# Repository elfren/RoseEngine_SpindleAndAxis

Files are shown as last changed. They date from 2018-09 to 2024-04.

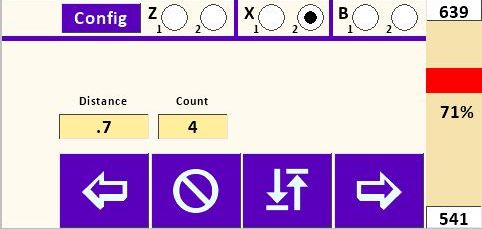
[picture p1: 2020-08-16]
MDF Rose Engine 2.0/Nextion Multiple Stepper Control User's Guide/Images/Nextion-Move2.jpg

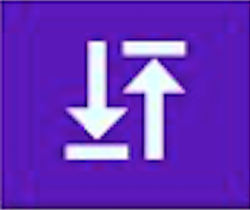
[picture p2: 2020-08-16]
MDF Rose Engine 2.0/Nextion Multiple Stepper Control User's Guide/Images/ButtonMove-Return.png

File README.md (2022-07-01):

# RoseEngine_SpindleAndAxis
Drive Rose Engine steppers for the spindle and up to 4 additional axes.

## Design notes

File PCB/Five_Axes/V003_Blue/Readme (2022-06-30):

This pcb uses several surface mount components (see BOM).
https://www.seeedstudio.com/5-axes-Rose-Engine-and-CNC-g-1367637

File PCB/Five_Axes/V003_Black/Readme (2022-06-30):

This 5 axes Rose Engine and CNC controller uses all through hole components.
SeeedStudio: https://www.seeedstudio.com/Rose-Engine-5-motor-driver-g-1364994
OshPark: https://oshpark.com/shared_projects/8f3nmKMy

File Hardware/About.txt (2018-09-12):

GT2-5mm 108 tooth pulley designed for CNC milling.

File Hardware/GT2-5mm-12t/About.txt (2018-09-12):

Print at 100% infill using ABS filament.

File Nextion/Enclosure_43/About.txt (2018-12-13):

Print at 30% to 100% infill.
Note: The bezel only has one hole created for the Nextion.  The other three need to be drilled (2.5mm) and all four should be tapped (3mm).

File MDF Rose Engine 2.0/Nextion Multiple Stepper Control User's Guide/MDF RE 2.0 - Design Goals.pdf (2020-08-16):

# MDF Rose Engine Lathe 2.0

# with Stepper Motor Drive

# Design Goals

## Version 1.0 04 July 2020

## MDF Rose Engine 2.0 – Design Goals

This document is intended to outline the design goals around which the machine is specified.

If you have any questions, please contact us at ColvinTools@Gmail.com.

Good luck.

Rich Colvin & Jack Zimmel

### Table of Contents

## Guiding Principles

### General – Target User

1. The target user for the MDF rose engine lathe is
a. An experienced wood turner, with
b. The basic woodworking skills that would have been garnered in shop class.
2. The design will ensure it can be built by the woodworker:
a. Using a kit of parts we will provide,
b. Possessing basic woodworking skills, and
c. Using tools which can reasonably be expected to be available or easily accessible.

### General – Overall Design

1. The intent is to stay consistent with the original overall design outlined by Jon Magill, especially the designs built into the rosettes.
2. The design will continue to use MDF as the primary building material for the headstock and base.
3. The design will include commonly implemented updates to the original design, including:
a. Stepper motor for the spindle drive,
b. Metal sheet on the lathe’s bed,
c. Magnetic hold-downs (MagSwitches) for locking the cross slide into position on the lathe bed,
d. Front and rear rubbers, and
e. Amplitude adjusting (front rubbers only).
4. The design will not include previously offered features which would make the overall design cumbersome or expensive. In particular, hand cranking capabilities will not be included,
5. The design will provision for known future options / expansions:
a. Multiple stepper motors with controls for the multiple stepper motors, and
b. Pumping on the spindle.

### Kit Offered for Sale

1. The design should enable a complete rose engine lathe to be built from a kit for less than $2,000. And the design should be designed to be lower if the user opts to make their own parts.
2. The kit offered for sale will provide options which, in total, will supply the hobbyist with all the parts needed (including the MDF).
a. Using standard, off-the-shelf parts, with a conscious decision being made when customized parts are to be used,
b. Sourcing parts from vendors likely to provide the parts for a reasonable time into the future (i.e., minimizing rework of the designs), and
c. Sourcing more expensive parts from vendors who will accommodate drop-shipments. This reduces the investment in inventory for the provider of the kits.
3. The kit offered for sale will provide options where it makes reasonable sense. Option selections include:
a. Spindle drive option – Everything needed to drive the spindle with a stepper motor (stepper motors allow the spindle's speed to be slowed down to multiple minutes per revolution)
i. Or allow the builder to build or source their own approach, and
ii. Also, provision existing MDF rose engine lathe owners to add this to their system.
b. Cutting frame option - Enabling the builder to
i. Select a universal cutting frame with an integrated motor,
ii. Select a universal cutting frame with an overhead drive,
iii. Make their own cutting (or drilling frame), or
iv. Source one from a different source.
c. Tool holder (cross slide and tool post) option – Enabling the builder to
i. Select a pre-defined set of cross slide, quick-change tool post, and tool holders (AXA), or
ii. Source one from a different source.
d. Case Option – Enabling the builder to
i. Select a pre-cut MDF kit with all the pieces for the body and headstock, already cut to size and ready for assembly
ii. Source and build the case and headstock on their own.

## Design Criteria

### Headstock

1. The distance from the center of the rocking pivots to the center of the spindle shall be 12 inches. The rosettes are designed around this.

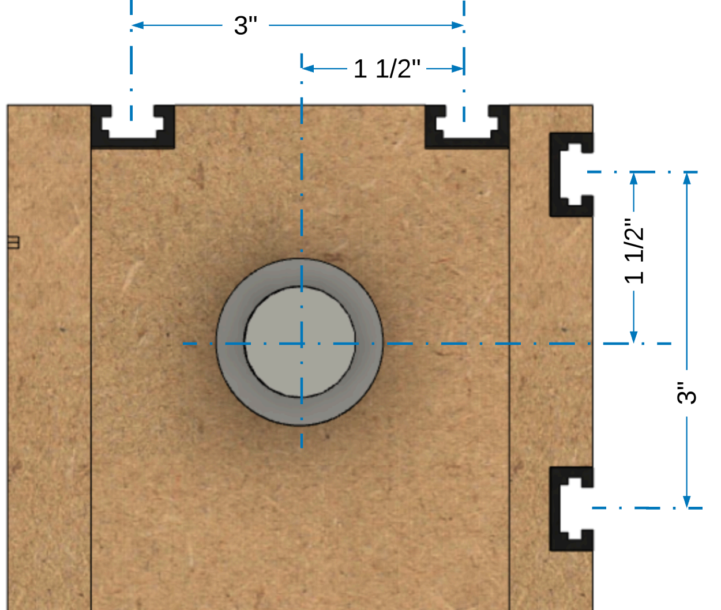
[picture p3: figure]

2. The rocking pivot points are to be aligned so
that the rotation of the headstock is fully
aligned with the rotation of the spindle.
3. T-Tracks will be implemented on the headstock for standardized add-ons.
a. The T-Tracks will be aligned to be parallel with the spindle,
b. The center of each T-Track shall be 1-1/2” from the center of the spindle (as shown to the right),
c. There shall be two T-Tracks on the top of the headstock, and
d. There shall be two T-Tracks on the rear of the headstock.

### Base

1. The lathe’s bed shall be sized to accommodate the
attachment of a 24” x 24”
sheet of steel.
2. The sheet of steel on the lathe bed shall be minimally 16
gauge, and the design shall be able to accommodate
upgrading that sheet to a
thickness of 1/8”.
3. The lathe’s bed (B1 / B1A) shall:
a. Overhang the base by
2” on the front, back,
and right sides (in the

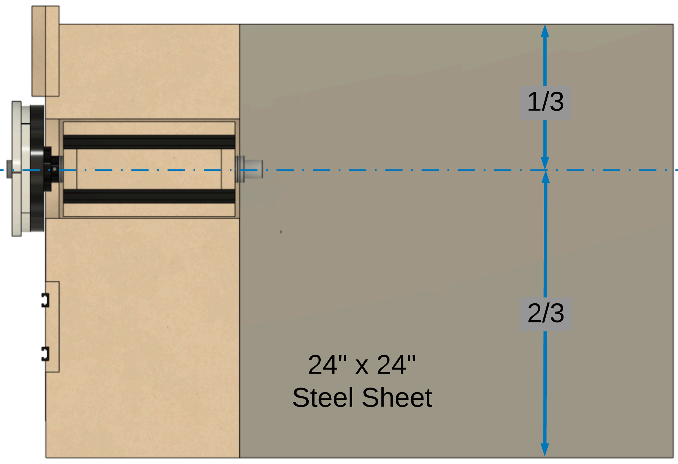
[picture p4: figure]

picture to the right, those are the right, top, and left sides),
b. Be flush against the left side (B3 / the rubber support post), and
c. Be positioned front-to-back so that it has approximately 1/3 behind the spindle’s axis of rotation, and 2/3 in front of that axis.

### Spindle Drive

1. The spindle drive shall use a NEMA 23 stepper motor.
2. The controls will be implemented the Teensy/Nextion controls.
a. The power supply (EDR-120-24) will be expandable as necessary for future options.
b. The design will be based on the DM542T motor drivers; however, the user could opt to use other drivers such as the DRV8825.
3. The connectors for the stepper motors and aviation plugs with 4-wire connections.

### Other

1. Tool holding is designed around the AXA standard.

To the extent that material may appear to be infringed, we assert that such alleged infringement is permissible under fair use principles in U.S. copyright laws. If you believe material has been used in an unauthorized manner, please contact me at ColvinTools@Gmail.com.

Portions of this document are copyrighted by Jon Magill and are used with his permission.

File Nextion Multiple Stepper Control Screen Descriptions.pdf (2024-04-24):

## Nextion Multiple Stepper Control Screen Descriptions

V: 3.1.0

Splash Screen

Purpose: Initialize program

Buttons explanation: Touching one of the top or bottom row buttons will take you to that screen.

Main Screen

Purpose: Allows direct control of spindle speed and direction and auxiliary axis speed and direction independent of one another. Typically used for continuous spindle and/or continuous Axis motion (turning or facing cuts, continuous rose engine patterns on cylindrical or face surfaces., etc.).

Buttons explanation:
- “” (Counterclockwise) and “” (Clockwise) rotational arrows indicate direction of the Spindle. “”(In) and “”(Out) indicates direction of the selected axis. Rotation/movement continues until “” (Stop) is pushed.

- Right and left speed bars (for Spindle and Axes, respectively, are shown as a percentage of maximum speeds set for “Main” and “Z, X, M3 or M4 Axes”. Max speed and acceleration entry fields are shown at the top and bottom of each speed bar. They are in stepper steps per second.
- “ “(Return): Returns the spindle or the selected axis to the start point of the previous operation.
- Synchro: Runs the spindle and M3 synchronously at the specified percentages. Negative number runs the spindle and M3 in opposite directions.

Number Pad Screen

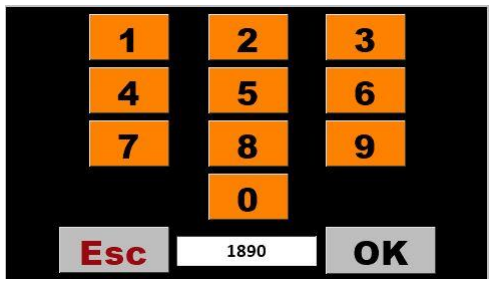
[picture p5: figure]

Purpose: This screen appears whenever any numerical value on any screen is tapped. Revise the number in the box by tapping the box multiple times to “backspace” over each digit or decimal point, and then re-enter the new value using the number pad buttons. Pressing “OK” saves the number back to the value box on the previous screen and returns user to that screen.

Synchronization Screen

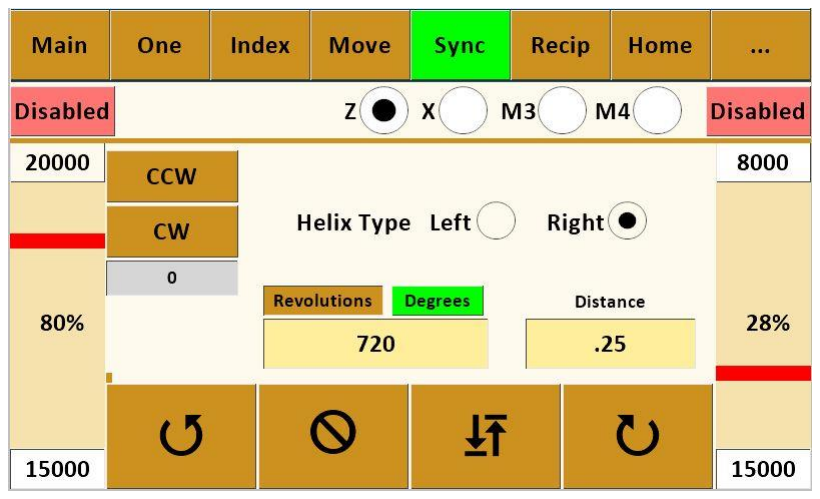
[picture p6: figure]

Purpose: Synchronizes the Spindle and Auxiliary Axis to produce helical patterns or threads on cylindrical surface of workpiece or to produce spirals on a face surface.

Buttons explanation:
- “Left” and “Right” determine whether helix runs clockwise or counterclockwise on the piece.
- “CW” (Clockwise) and “CCW” (Counterclockwise) index the spindle for the next cut path – either clockwise or counterclockwise per user design. Amount the spindle will index uses the value in “Size” set in the box on the Index #1 Screen (this value could be either in divisions of a circle or degrees depending upon which option is toggled on Index #1 Screen).
- “Revolutions or Degrees” variable value determines how far around the piece the helix will travel based on the spindle rotating. The value of 4 illustrated will rotate spindle 4 revolutions while the value 720 will rotate the spindle 720 degrees.

- “Distance” variable value determines the cut length (amount of Z axis movement) and is dependent upon value entered in Setup Screen for “Distance/360”.
- Right and left speed bars (for Spindle and Axis, respectively, are shown as a percentage of maximum speeds set on the Configuration Screen for “Sync” and “Z Axis”, respectively. Note that slowest value on speed bars will “control” the other value.
- “”(In) and “”(Out) determine whether cut is made toward or away from headstock. Pattern will run the pre-determined “Distance” and then stop and wait for return direction instruction. User chooses whether to cut in both directions or retract cutter and return to start without cutting.
- “ “(Return): Returns both the spindle and the axis to the start point of the previous operation.
- See appendix for procedure for using the Synchronization Screen for thread cutting.

Reciprocation – Axial

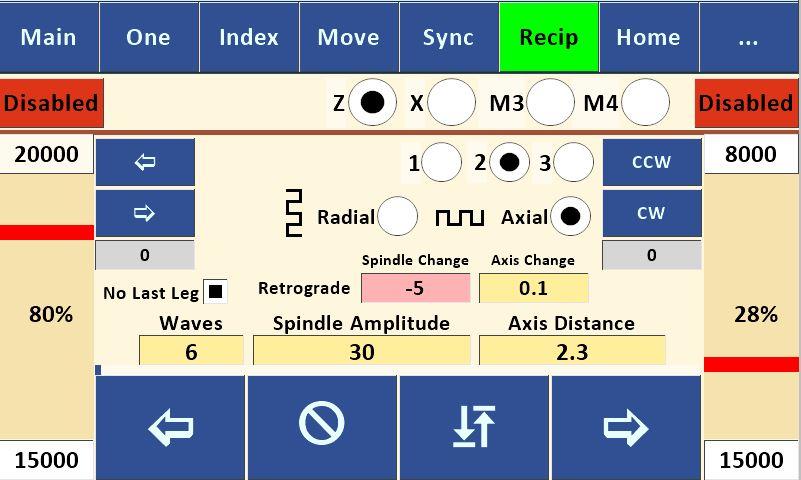
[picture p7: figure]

Purpose: Synchronizes Spindle and Auxiliary Axis to produce a reciprocating pattern along the longitudinal cylindrical surface of workpiece: It works by reversing spindle direction alternately while Z or X axis continues in the same direction.

Buttons explanation

- “1” Pattern is an equal angle on the up and down legs.
- “2” Pattern is a square wave.
- “3” Pattern is a like a sawtooth. The up leg is angled, the down leg is straight down.
- “CW” (Clockwise) and “CCW” (Counterclockwise) index the spindle for the next reciprocating cut path – either clockwise or counterclockwise per user design or desire. Amount the spindle will index uses the value set in the “Size” box on the Index #1 Screen (this value could be either in divisions of a circle or degrees depending upon which option is toggled on Index #1 Screen).
- “Wave Count” variable sets number of individual waves /\ to be cut along the cylinder.
- “Spindle Amplitude” variable sets “height” of each wave in degrees of rotation.
- Retrograde changes the length of each leg by the specified amount either plus or minus.
- No Last Leg removes the final leg of a Square wave (pattern 2).
- “Axis Distance” variable determines the cut length for entire pattern (amount of Z, X, M3, or M4 axis movement) and is dependent upon value entered in Setup Screen for “Distance/360”.
- “”(In) and “”(Out) determine whether cut is made toward or away from headstock. Note that “”(In) starts with a downward move and “”(Out) starts with an upward move (test your individual machine and apparatus to verify – your results may vary). Pattern will run the pre-determined “Axis Distance” and then stop and wait for return direction instruction. User chooses whether to cut in both directions or retract cutter and return to start without cutting.

- “ “(Return): Returns both the spindle and the axis to the start point of the previous operation.

Reciprocation –Radial

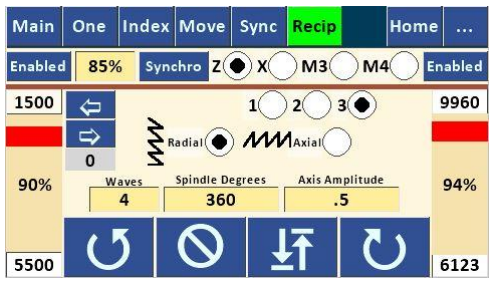
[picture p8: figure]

Purpose: Synchronizes Spindle and Auxiliary Axis to produce a sharp-pointed reciprocating pattern along the circumferential surface of a cylindrical workpiece: It works by alternately reversing Z or X axis direction while spindle continues rotating in the same direction.

Buttons explanation
- To navigate to this screen, start with “Recip” and toggle from Axial to Radial.
- “1” Pattern is an equal angle on the up and down legs.
- “2” Pattern is a square wave.
- “3” Pattern is a like a sawtooth. The up leg is angled, the down leg is straight down.
- Small “”(In) and “”(Out) move the Z or X axis to the next pattern starting position. Z or X axis movement will be the value of “Distance” set on the Move Screen for that axis.
- “Return” button rotates the spindle to the pattern start point.
- “Acceleration” and “Speed” values for this screen are set here for both Spindle, Z, and X axes. See notes on value limitations under Configuration Screen explanation. Because of synchronization of the spindle and Z or X axis speeds, one of the maximum speeds will control the other.
- “Wave Count” variable sets number of individual waves ( > ) to be cut along the cylinder.
- “Spindle Degrees” variable sets the circumferential distance around the cylinder for the total pattern. Entering 360 would wrap the pattern all the way around the cylinder; entering 90 would condense the whole pattern around just 90 degrees of the cylinder.
- “Axis Amplitude” variable sets “height” (distance along Z, X, M3 or M4 axis) of each wave and is dependent upon value entered in Setup Screen for “Distance/360”.
- | Large “”(In) and “”(Out) buttons determine the direction of cut around the spindle. | Pattern will run the
pre-determined “Spindle Degrees” then stop and wait for return direction instruction. User chooses whether to cut in both directions (either on the same cut path or on subsequent path) or retract cutter and return to the origin point without cutting.
- “ “(Return): Returns both the spindle and the axis to the start point of the previous operation.

One Screen (Single Stepper Screen)

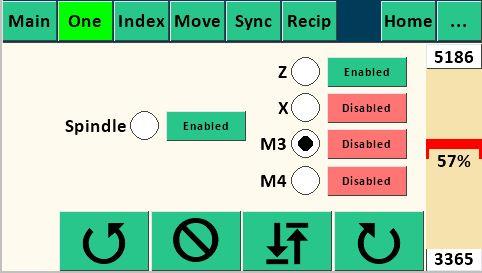
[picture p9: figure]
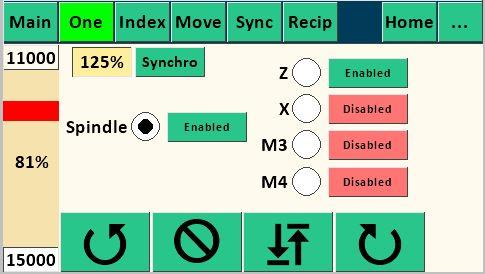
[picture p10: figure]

Purpose: Allows control of either the spindle or a single axis speed and direction. Useful for secondary spindle operation such as higher or lower speed functions than the Main Screen.
Buttons explanation
- “Enabled” shows status (either “Enabled” or “Disabled”) of either Spindle stepper motor or an Axis stepper motor as selected. If enabled, the motor is in locked status; if disabled, the selected motor can be repositioned. Default is “Disabled”. Primary use for these buttons is to lock the spindle or axis while performing another operation.
- “” (Counterclockwise) and “” (Clockwise) rotational arrows indicate direction of the Spindle .“”(In) and “”(Out) buttons indicate direction of an axis. Movement continues until “Stop” is pushed.
- Speed bar is shown only for the selected axis or spindle.

Index Screen

Purpose: Allows indexing spindle for use in index work or other uses. Buttons explanation

- 1-5: Individual indexes
- “Div” radio button sets the indexing to number of divisions of a full rotation, toggling to “Deg” sets the indexing to number of degrees.

- “Index” box shows current completed index
- “Next Index” shows ID of the next index. It will show lower ID if the CW button was last touched and higher if CCW button was touched
- Speed bar is shown as a percentage of maximum speeds set on the Configuration Screen for “Index”.
- “Divisions” of a circle or “Degrees”, depending upon which is toggled. Note that the value of the selected index (1 through 5) is used by the “CW” and “CCW” indexing movements on the Synchronization Screen and the Reciprocation – Axis Screen in either “Divisions” or “Degrees”, depending upon which is toggled.
- M3 and M4 will only be shown if they are set to Radial on their respective configuration screens.

Index Screen with file dropdown open

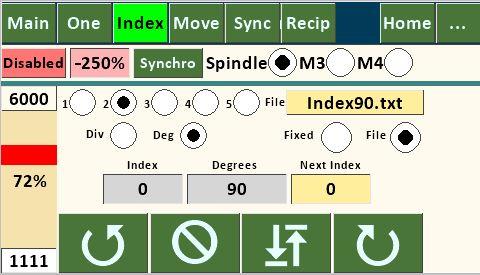
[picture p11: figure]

Purpose: Allows variable index sizes to be retrieved sequentially from a file stored on a microSD card. This feature could be used to place evenly spaced features (such as barleycorns) around the circumference of an ellipse (i.e. equal division of the ellipse), with the angular movement in degrees precalculated using a CAD program.

Selecting the filename text box will open a dropdown list of files located on the microSD card. Use the Up and Down arrows to traverse the file list. While the dropdown list is active, all other controls on the page are disabled. The dropdown list can be closed either by selecting a file, or by touching the Filename textbox. Each Index may have its own file.

The file format is ASCII text (numbers, letters, and decimal only) with each number on a new line, saved to the microSD card using a separate computer. Because the SD Card library only supports the 8.3 or Short File
Name convention, the file name must be a maximum 8 characters + a period + three-character extension (thus the 8.3); the name is not case sensitive. It's not necessary to have the extension, but the limit for the name is 8 characters when no extension is used. Multiple files can be loaded onto the microSD card for use on one or more work pieces as desired.

The counterclockwise and clockwise arrows determine direction of spindle movement during indexing. When using the “File” version, each successive index will read successive file numbers off the microSD card (in either “Div” or “Deg” as selected on this screen). When the end of the file is reached, “Size” will be reset to 0. The “Index” value will be increased when indexing clockwise and decreased when indexing counterclockwise. The read position of the file can also be set by editing the “Index” value.
The “Div” and “Deg” radio buttons and the “Enabled” button work the same as on the other Index screens above.

Move Screen

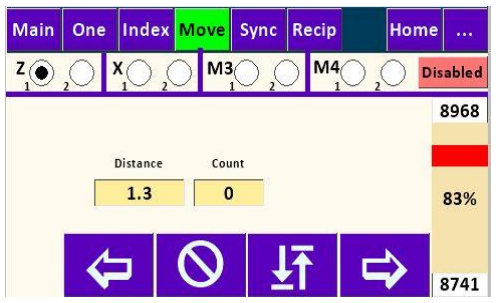
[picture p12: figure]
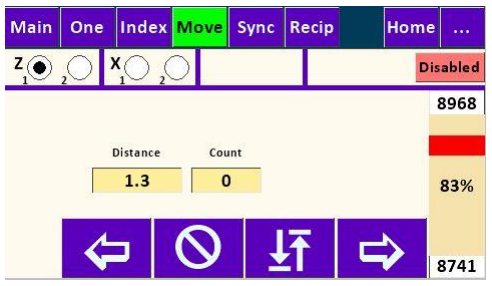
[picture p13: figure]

Purpose: Moves the Z or X Axis a specific distance and direction. This could be used to cut a flute or other element along Z Axis of specific length, or used on the end face of a cylinder if set up to drive the X Axis, to move a specific distance to produce rose engine basket weave or other repeating design element on the cylindrical surface of the workpiece, or to plunge in and out of cylindrical surface to do index work if set up for X Axis. Each axis has two separate move settings.

Buttons explanation:
- “Distance” variable sets amount of movement along Z or X Axis and is controlled by Setup Screen Value “Distance/360”.
- “Count” tracks the number of moves.
- “Total” tracks total distance of movement (adding in one direction, subtracting in the other.
- “In” and “Out” indicate direction of the Axis movement. Movement will continue for “Distance” set and then stop and wait for another move instruction, either repeating move or returning to origin.
- Speed bar is shown as a percentage of maximum speed set on the Configuration Screen for “Z or X
Axis”.
- M3 and M4 will only be shown if they are set to Linear on their respective configuration screens.

Home Screen

The Home screen contains links to all of the pages.

Rose Screen

Purpose: Create Rose or single stage geometric chuck patterns, see Wikipedia Rose (mathematics). (https://en.wikipedia.org/wiki/Rose_(mathematics))

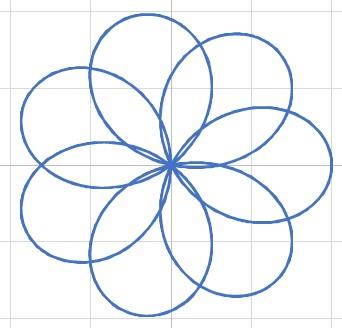
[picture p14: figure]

Buttons explanation:
- “n” numerator. Values may be integers or floating point.
- “d” denominator. Values may be integers or floating point.
- “k” ratio of n/d.
- “Amplitude” variable sets “height” (distance along Z or X Axes) of each lobe and is dependent upon value entered in Setup Screen for “Distance/360”.
- “” (Clockwise) and “” (Counterclockwise) rotational arrows indicate direction of the Spindle. Rose pattern continues until “Stop” is pushed.
- “ “(Return): Returns both the spindle and the axis to the start point of the rose pattern.
- Note: M3 or M4 axes only available when they are set to Linear on the M3 or M4 Axis Configuration page.

Grk (Greek Key or Meander) Pattern Screen

Purpose: Create Greek Key or Meander patterns. The Pattern page has six built-in patterns. Patterns are created by moving either the spindle or one of the axes individually.

Buttons explanation:

- Pattern: Create a Greek Key using one of the built-in patterns.
- File: Create a Greek Key by reading values from a file. See below.
- Radial or Axial: Creates a pattern radially (circumferentially) of axial.
- 4a and 4b: Create a pattern four segments wide. 4a is eight segments tall, 4b is thirteen segments tall.
- 3a and 3b: Create a pattern three segments wide. 3a is four segments tall. 3b is eight segments tall.
- 2a and 2b: Create a pattern two segments wide. 2a is three segments tall. 2b is six segments tall.
- Length: Specifies the length of the shortest Z or X axis segment. Each pattern will have segments which are a multiple of the shortest segment.
- Patterns Per 360: Specifies how many individual patterns will fit in 360 degree rotation of the spindle. This controls the length of the shortest spindle segment.
- Count: Determines the actual number of patterns to create. Setting it less than the Patterns Per 360 value will leave a space at the end of the pattern. Setting it larger will recut the same pattern. This is useful when you want to cut a pattern deeper. Grey box shows the current executing pattern count.

The following shows each pattern. The numbers by each segment indicate the length of that segment. The arrows show the direction the cutter is traveling. When the arrows change color it indicates the next segment’s direction.

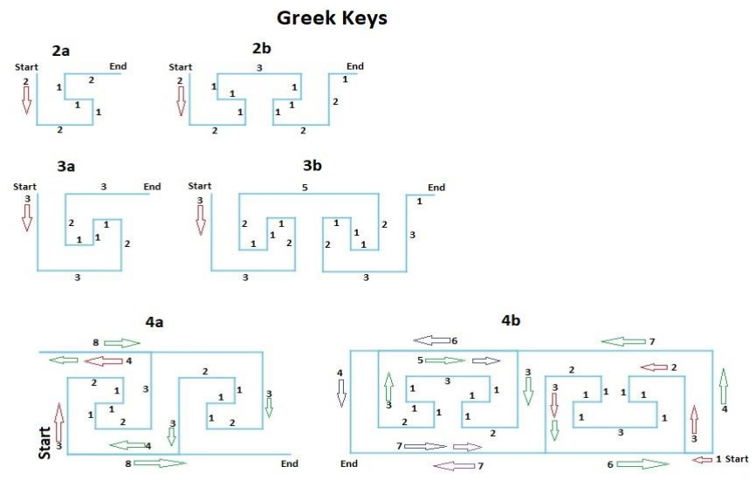
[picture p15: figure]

Program from File Screen

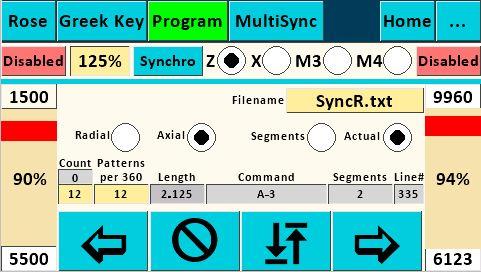
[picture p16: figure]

Purpose: Create Greek Key or Meander patterns by reading values from a file.

Buttons explanation:

- Filename must be in 8.3 format: 8 character name, a period, and a 3 character extension. It isn’t necessary to have the full 8.3 characters. Note: Apple computers may automatically add “.txt” to the name.
- Selecting the filename text box will open a dropdown list of files located on the microSD card. Use the Up and Down arrows to traverse the file list. While the dropdown list is active, all other controls on the page are disabled. The dropdown list can be closed either by selecting a file, or by touching the Filename textbox.
- Segments: Values in the file are interpreted as a multiplier of the “Length” for the Z, X, M3 or M4 axes and as a multiplier of the calculated segment size for the spindle. Floating point numbers are valid.

- Actual: Values in the file are used as the length of the move. Floating point numbers are valid.
- Grey boxes: Command, Segments, and Line# show the values for the current line in the file being executed. Count shows the current executing pattern count.

File format:
The file must be plain text (ASCII).
Each line in the file must begin with an axis identifier letter and end with the length of the move, except for the Comment and End lines.

Identifiers:
- ; Comment: Begins with a semi-colon, “;”, and may have up to 25 characters. There is no limit on the number of comment lines in a file. Each comment line must have a least one additional character.
- E End: Begins with a capital “E”. All files must have this as the last line in the file.
- WS(Plus count of vertical segments in the pattern). Required for all radial patterns.
- WA(Plus count of horizontal segments in the pattern). Required for all axial patterns.
- WB(Plus count of M3 radial segments in the pattern). Valid when M3 is Radial and rotating the workpiece. Do not use when M3 is Radial or Linear and driving a sliderest.
- WD(Plus count of M4 radial segments in the pattern). Valid when M4 is Radial and rotating the workpiece. Do not use when M4 is Radial or Linear and driving a sliderest.
The following commands can be interpreted as having a multiplier or as the actual size of the move.
- A(Plus multiplier or actual length) Negative number moves axis towards the spindle, positive moves away.
- S(Plus multiplier or actual length) Negative number moves spindle CCW, positive moves CW.
- H(Plus multiplier or actual length)V(Plus multiplier or actual length) Specifies a coordinated diagonal move with the spindle and the active axis. H is a horizontal move with the axis and V is vertical move with the spindle. Each move is a leg of a right triangle.
- P(Plus multiplier) Pause in seconds.
- O(Plus multiplier or actual length) Moves the cutter away from the workpiece.
- I(Plus multiplier or actual length) Moves the cutter into the workpiece.
- X(Plus multiplier or actual length) Moves X axis. Negative numbers reverse direction.
- Z(Plus multiplier or actual length) Moves Z axis. Negative numbers reverse direction.
- B(Plus multiplier or actual length) Moves M3 axis. Negative numbers reverse direction.
- C(Plus multiplier or actual length) Moves Spindle. Negative numbers reverse direction. (C is a rotary axis parallel to the spindle and to Z.)
- D(Plus multiplier or actual length) Moves M4 axis. Negative numbers reverse direction.
- T(Primary axis Id: BDSXZ B=M3,D=M4,S=Spindle,X, or Z) (Plus multiplier or actual length) Moves) (Secondary axis Id: BDSXZ B=M3,D=M4,S=Spindle,X, or Z) (Plus multiplier or actual length) Moves) This works similar to the HV command except you can specify which two axes(motors) you want to move. This allows Cartesian movements when the M3 or M4 are set to Linear, and Polar movements when they are set to Radial.

M3 Parameters
- JR – M3radius
M4 Parameters
- LR – M4Radius
Page commands. These use settings on the individual pages Q commands are deprecated.

- QM(Plus multiplier) Moves an axis using settings on the MOV page. -1 multiplier moves towards the headstock, 1 moves away from the headstock.
- QI(Plus multiplier) Index the spindle using settings on the IND page. -1 multiplier moves CCW, 1 moves CW.
- QR(Plus multiplier) Reciprocate using settings on the REC page. -1 multiplier moves towards the headstock, 1 moves away from the headstock.
- QS(Plus multiplier) Synchronize spindle and axis using settings on the SYNC page. -1 multiplier moves towards the headstock, 1 moves away from the headstock.
Page settings. These set parameters on the pages.
Sync page:
- GG(Plus multiplier) Synchronize spindle and axis using settings on the SYNC page. -1 multiplier moves towards the headstock, 1 moves away from the headstock.
- GH - Sync Helix Type 0=left 1=right
- GD - Sync Distance (floating point)
- GR - Sync Revolutions (floating point)
Recip page:
- VV(Plus multiplier) Reciprocate using settings on the RECIP page. -1 multiplier moves towards the headstock, 1 moves away from the headstock.
- VT - Recip Radial =0 Axial=1
- VK - Recip Style
- VW- Recip Waves (Integer)
- VS - RecipSpindle (floating point)
- VA - Recip Axis (floating point)
Move page:
- FF(Plus multiplier) Moves an axis using settings on the MOVE page. -1 multiplier moves towards the headstock, 1 moves away from the headstock.
- FD - Move Distance (floating point)
Index page:
- NN(Plus multiplier) Index the spindle using settings on the INDEX page. -1 multiplier moves CCW, 1 moves CW.
- NT - Index Divisions=1 Degrees=2
- NI - Index Division or degrees size (floating point)
- ND- Index Division or Degrees size (floating point)
- NJ - Index ID (Integer from 1 to 5)
Rose page:
- RR(Plus multiplier) Execute Rose page. -1 multiplier moves towards the headstock, 1 moves away from the headstock.
- RN - Set n.
- RD - Set d.
- RS - Set spindle revolutions.
- RA - Set axis distance.

Enable/Disable Steppers
- KS(Plus multiplier) Enable or Disable Spindle. Disable = 0, Enable =1.
- KX(Plus multiplier) Enable or Disable X Axis. Disable = 0, Enable =1.
- KZ(Plus multiplier) Enable or Disable Z Axis. Disable = 0, Enable =1.
- KB(Plus multiplier) Enable or Disable M3 Axis. Disable = 0, Enable =1.

- KD(Plus multiplier) Enable or Disable M4 Axis. Disable = 0, Enable =1.
•
- KA(Plus multiplier) Enable or Disable current Program page axis. Disable = 0, Enable =1.
- Note: Steppers are automatically enabled when executing a command, so it is not necessary to enable one after disabling it.

Example file:

;Pattern 2a
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
MultiSync Screen

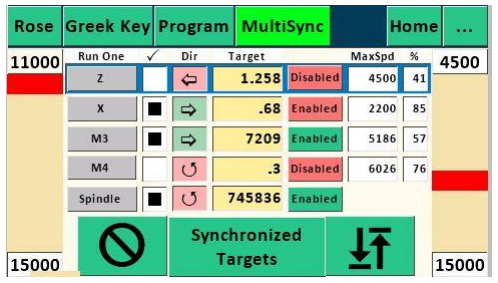
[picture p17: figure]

Purpose: Run multiple motors synchronously or individual motors continuously.

Buttons explanation:
- Grey buttons run the selected axis in continuous mode. Motor will run until Stop is pressed.
- Check column: Selected axes are run synchronously until each reach the Target.
- Dir column: Indicates direction motor will run.
- Target column: Target distance, may be either lineal or radial depending on the settings on M3 or M4 pages. Radial targets are in degrees. Lineal in distance.
- Enable/Disable column: Enables or disables the stepper motor.

Preferences Screens

Purpose: The factors on these screens control how speeds and distances are determined. The left columns show settings on the Nextion. Touching one of the text boxes allows you to edit that value. The right columns show settings stored on the Teensy. These are read only and should match the left column settings.

Spindle

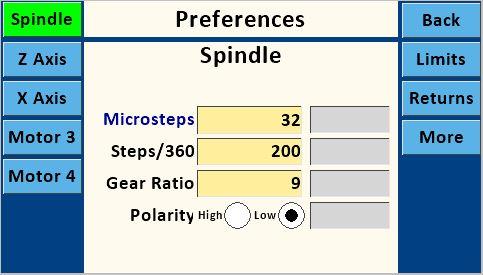
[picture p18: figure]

Buttons explanation:
- The software is currently set up for 32 Microsteps, 200 Steps/360, and 9 Gear Ratio for the spindle. This assumes a stepper motor with 200 steps per revolution and is the “standard” configuration for the
MDF Rose Engine with a 12 tooth spindle motor drive pulley and 108 tooth driven pulley yielding a Gear Ratio of 9. Once set, the values for the Spindle will remain the same unless changes are made to spindle drive setup.

Z Axis

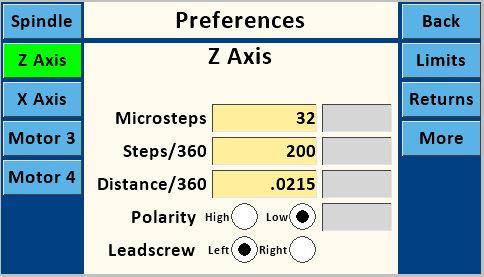
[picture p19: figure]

- The Z axis screen shows 32 Microsteps, and that you are using a stepper motor with 200 Steps/360. This is intended to show microstep values must use valid values for the stepper driver, usually 1, 2, 4, 16, 32, 64, and
128. These settings must match the jumper settings on the PCB.
- The “Distance/360” is the distance the Z axis carriage moves in one revolution of its stepper motor. It is a value arrived at empirically by measuring the movement of the Z Axis using a dial indicator or other appropriate device while the stepper motor revolves a set number of turns. This can be accomplished by entering a value in “Distance/360” such as 1, then using the Move Screen to move a “Distance” of 20 while measuring. This should turn the motor through 20 full revolutions. Divide the distance traveled by 20 and enter calculated value into “Distance/360”. If the total distance moved in 20 revolutions is insignificant, use a larger “Distance” number like 50 (or even 100). Note that best practice is to remove backlash from the Axis mechanism prior to the measurement run by moving the axis in the same direction. It may be possible to get a starting point for Distance/360 by calculation calculating the stepper pulley to driven pulley ratio, and/or the thread pitch.

Finally, it’s important to note that if you use different pieces of apparatus (such as a cross-slide, a spherical or a curvilinear apparatus) with the Z Axis, each will likely have a different value for Distance/360, so keep track of these separately for each piece of apparatus (See Load Ini section).
- The Enable “High” and “Low” radio buttons for both Spindle and Z Axis are set to “Low” by default, which is the correct setting when using the DRV8825 Stepper Drivers. The “High” setting is for use for some external stepper drivers.
- “Hand” should be set to the thread direction of the axis leadscrew. If using a Hardinge compound sliderest with a left-hand thread, for example, set “Hand” to “L”. If using an apparatus with a righthand threaded rod, set “Hand” to “R”. Test to verify.
- “Back” button returns to the previous screen.
- “Limits” button activates the Limits Screen.
- “Returns” button activates the Returns Screen.
- “Refresh”: Retrieves settings stored on the Teensy. These settings should match the left columns which are stored on the Nextion.

X Axis

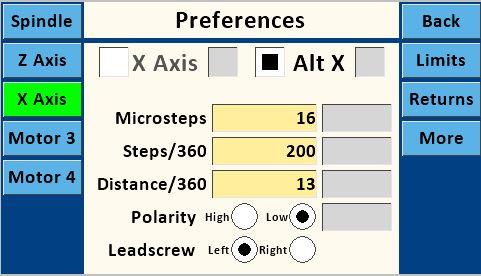
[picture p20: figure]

- The X axis can use two different steppers. Alternate X will usually be used to adjust a curvilinear arm while the main X axis is floating.

M3 Axis

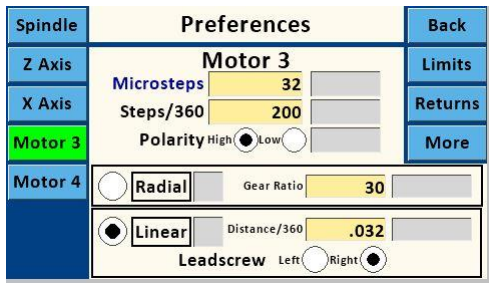
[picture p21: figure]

- The M3 Axis can be configured as either a radial axis, like a spherical apparatus or a spindle, or as a linear axis. When configured as a radial axis for a spherical device it uses a calculated distance along the circumference based on the radius length between the spherical device pivot point and the cutter. The ‘M3 Radius’ text box will appear on a page when the M3 axis is active and the M3 axis is set to Radial.

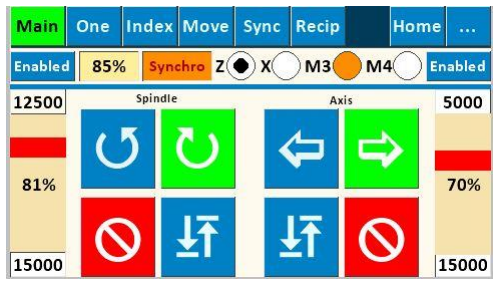
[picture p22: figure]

M4 Axis

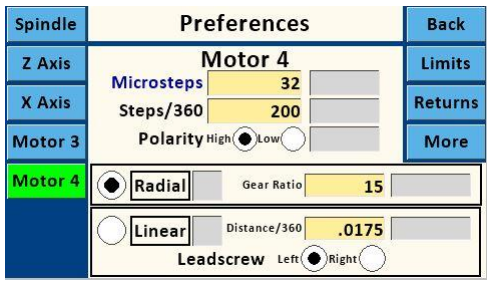
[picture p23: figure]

- The M4 Axis can be configured as either a radial axis, like a spherical apparatus or a spindle, or as a linear axis. When configured as a radial axis for a spherical device it uses a calculated distance along the circumference based on the radius length between the spherical device pivot point and the cutter. The ‘M4 Radius’ text box will appear on a page when the M4 axis is active and the M4 axis is set to Radial.

Limits screen

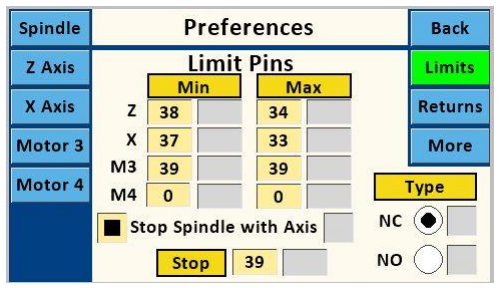
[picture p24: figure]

Purpose: Set pin numbers for limit switches.

Limit switches and Estop switch(s) can be wired either normally closed or normally open. Normally closed is recommended. Multiple switches may be wired together serially, not parallel.

When a limit switch is triggered, the action button for that direction limit switch will turn red. No further action can be taken until the “” (Stop) button is touched. Once that is done, the opposite direction action button can be touched while the limit switch is still closed.

Limit Max triggered:

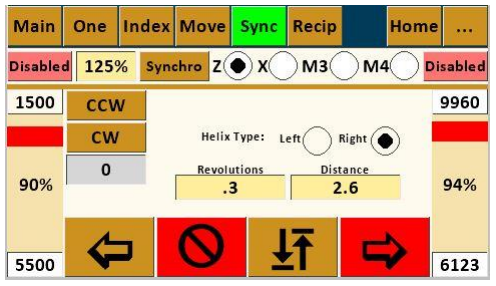
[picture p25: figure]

Limit Min triggered:

When EStop switch is triggered, the action buttons will turn red. No further action can be taken until one of the “” (Stop) buttons is touched and the EStop switch is not closed.

Returns screen

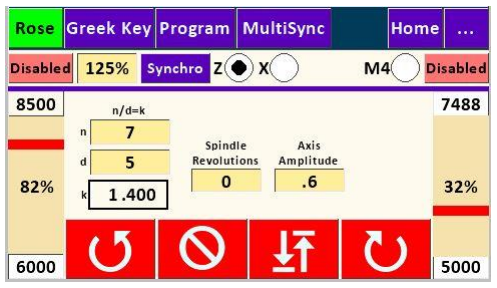
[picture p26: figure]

Purpose: Set speed and acceleration for return actions.

More screen


Screen Brightness slider will change the brightness of the screen.

The ‘Show BE’ button will open the BE page.

‘EEPROM’ button shows the values stored in EEPROM on both the Nextion and Teensy. It is used to verify the settings match. Mismatches can occur when updating the software.

The ‘Load Ini’ button will open the Load Ini page.

Load Ini screen

Touching the Load Ini button will download settings from the specified .ini file. Settings are shown in the grey boxes as they are updated. Custom settings may be stored in multiple .ini files.

The other buttons will change the display to the specified page. .

EEPROM screen


Nextion settings are shown in yellow, Teensy in grey.

will load motor settings from an ini file. Restarting the program may be necessary for the settings to be active. While Load Ini is running, the Key, Setting, and Value fields will show the current values being updated.

B&E screen

Currently under development. Only the Begin and End text boxes are active. They show the distance or degrees an axis or the spindle has moved from the start of the last operation on another screen. This can be used to verify the specified movement matches the actual movement.

# Appendix

General Notes:

1. When first setting up or when updating Teensy or Nextion software, go to each screen in turn and refresh all settings by entering new or current values in the text boxes and pressing “OK”, cycling the radio buttons, and moving the speed sliders.
2. X, Z, and B axes for the lathe in descriptions above use the | standard shown
here:

## Exercises

I. Thread Cutting for Boxes with the Synchronization Screen:
Note: refer to instructions in other resources (such as “Turning Threaded Boxes” by John Swanson, Schiffer Publishing, 1999) for box threading tips and techniques.

Example 1: Single-start thread of 16 threads per inch (1/16” pitch).
1. Set “Revolutions” to number of threads to be cut around the cylinder. Suggest using “4” as a starting point.
2. Set “Distance” to .25 (four threads at 1/16” = ¼”).
3. With a 60-degree double angle cutter running in a drilling frame set parallel to the lathe’s spindle and driven by the overhead, test and adjust Spindle and Axis speed bars as necessary to get a usable combination of feed and speed (not so fast as to bog down cutter, not so slow as to burn the wood). If necessary, adjust “MaxSpd” setting on Configuration Screen to get usable combination.
4. Test “Left” and “Right” radio buttons to determine which type of thread will be cut (left hand or right hand).
5. Choose whether to cut “In” or “Out” based on what makes sense for your piece.
6. Cut thread. Typical good practice uses roughing and final cuts for each thread. If wood tends to fuzz up or chip out, it’s common practice to flow some CA glue into the rough threads and let it cure prior to the final cut.

Example 2: Four-start thread of 16 threads per inch (1/16” pitch, ¼” lead)
1. Set “Revolutions” to number of threads (of each start) to be cut around the cylinder. Suggest using “1” as a starting point.
2. Set “Distance” to .25 (1/4” lead). This will cut one continuous thread traveling ¼” as it goes once around cylinder.
3. Got to Index #1 Screen. Select “Div” toggle and set value in “Size” box to “4”. Note: would also work to select “Deg” toggle and set value in “Size” box to “90”.
4. Follow steps 3, 4, 5 & 6 in Example 1 above.
5. Return to starting point with cutter retracted from work using “In” or “Out” as appropriate.
6. Index spindle using either CW or CCW based on personal preference to get to starting point of next thread start. Re-engage cutter and repeat cutting process(es) in step 6 in Example 1 for Start #2. Retract cutter and return to start point of Start #2.
7. Repeat indexing and cutting procedures for Starts #3 and #4.

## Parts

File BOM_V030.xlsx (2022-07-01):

Bill of Materials for Stepper Control Board Assembly
General
Quantity | Part # | Specification | Link | Comment
1 | Teensy 3.2, 3.5, or 3.6 |  | https://www.pjrc.com/store/teensy35.html | Also available on Amazon
1 | Nextion 4.3" Enhanced |  | https://nextion.tech/datasheets/nx4827k043/ | Also available on Amazon
Optional | Nextion 7 Intelligent |  | https://nextion.tech/datasheets/NX8048P070-011R/ | Also available on Amazon
Optional | Nextion enclosure |  | https://github.com/elfren/RoseEngine_SpindleAndAxis/tree/master/Nextion/Enclosure_43
1 | Power Supply | 24V, 5amp | https://www.amazon.com/gp/product/B01DLIYOYK/ref=ppx_yo_dt_b_search_asin_title?ie=UTF8&psc=1
1 | 30mm fan |  | https://www.amazon.com/Dorhea-Raspberry-30x30x7mm-Brushless-Cooling/dp/B07G97L9TL | Cooling stepper drivers
1 | MicroSD card | 32gb or smaller
1 | Micro USB cable |  |  | Must be data cable
1 | DC power plug | Panel or inline | https://www.amazon.com/VizGiz-Connector-5-5x2-1mm-Terminal-Replacement/dp/B07MPS3QD8?keywords
23 | Ferrule | 24 gauge | https://www.aliexpress.com/item/32584059579.html?spm=a2g0s.9042311.0.0.27424c4d0Ks7gC
 | Shielded 4 conductor 22 gauge wire | 15-20 feet
5 | GX12 connectors |  | https://www.aliexpress.com/wholesale?catId=14190101&initiative_id=AS_20200218181732&origin=y&SearchText=gx12 | GX16 may also be used
PCB -V003_Black
 | Description | Manufacturer Part Number | Link | Comment
4 | Stepper driver | DRV8825 | https://www.pololu.com/category/154/drv8825-stepper-motor-driver-carriers-high-current | May also use external drivers like DM542T
1 | DC-DC down converter | R-78E5.0-1.0 | https://octopart.com/search?q=R-78E5.0-1.0&currency=USD&specs=0
2 | Molex | 22272041 | https://octopart.com/search?q=22272041 | For external drivers add 5
1 | Resistor: 10kΩ (.25W) | CFR50J10K | https://octopart.com/search?q=cfr90j10k&currency=USD&specs=0 | R1, R3, R4, R5 resistors are not used.
6 | Electrolytic Capacitor: 100µF 50V | KM101M050F115A | https://octopart.com/search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 | https://www.amazon.com/gp/product/B01FDD48MY/ref=ppx_yo_dt_b_search_asin_title?ie=UTF8&psc=1
6 | Phoenix Male Terminal block 3.5mm (4 pin) | 1840382 | https://octopart.com/search?q=1840382&currency=USD&specs=0 | https://www.aliexpress.com/item/32584933839.html?spm=a2g0s.9042311.0.0.27424c4dsff8YN
Optional | Phoenix Male Terminal block 3.5mm (2 pin) |  |  | Only used for external 5V power supply.
7 | Phoenix Female Terminal block 3.5mm | 1897115 | https://octopart.com/search?q=emc+1897115&currency=USD&specs=0 | https://www.aliexpress.com/item/32584933839.html?spm=a2g0s.9042311.0.0.27424c4dsff8YN
2 | Dip Socket 20 pin | D2820-42 | https://octopart.com/search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
2 | Level Shifter | 74HCT245 | https://octopart.com/search?q=74HCT245&currency=USD&specs=0 | DIP-20 version
4 | Female header .100" | Conn_01x12_Female Pitch_2.54mm | https://www.amazon.com/2-54mm-Breakaway-Female-Connector-Arduino/dp/B01MQ48T2V
10 | Female header .100" | Conn_01x8_Female Pitch_2.54mm | "
2 | Female header .100" | Conn_01x6_Female Pitch_2.54mm | "
18 | Female header .100" | Conn_01x4_Female Pitch_2.54mm | "
2 | Female header .100" | Conn_01x2_Female Pitch_2.54mm | "
2 | Female header .100" | Conn_02x5_Female Pitch_2.54mm | "
3 | Jumper | Jumper_01x3_Male Pitch_2.54mm | "
8 | Male header .100" | Conn_01x5_Male Pitch_2.54mm | "
5 | Male header .100" | Conn_02x3_Male Pitch_2.54mm | "
18 | Jumper for 2.54mm Header (shunts) |  | https://www.aliexpress.com/item/32265972623.html?spm=a2g0s.9 | https://vetco.net/products/0-1-2-54mm-shunt-jumper/vupn8912
Stepper Motor Spindle Drive Materials
1 | Stepper motor | 180 oz-in, 2 amp current in Bipolar Series | https://www.amazon.com/Shaft-Stepper-1-26Nm-179oz-Router/dp/B01L3QVV66
 | Mounting plate |  | http://www.whidbeyworks.com/root/Resources_files/Headstock%20Modifications_v2.pdf
 | Idler and bearings |  | http://www.whidbeyworks.com/root/Resources_files/Headstock%20Modifications_v2.pdf
 | Mounting hardware
 | 12 tooth GT2-5mm pitch pulley to fit NEMA 23 motor shaft
 | 108 tooth GT2-5mm pitch pulley with rosette mounting and phasing holes. Jon Magill design
1 | Spindle drive belt | Gates 650mm length, 5mgt-09mm (130 teeth) | https://www.royalsupply.com/store/pc/Gates-650-5MGT-09-PowerGrip-GT3-Synchronous-Belt-5MM-Pitch-9400-6130-p17416.htm | https://offroadbelts.com/product/dd-powerdrive-650-5m-09-timing-belt
Stepper Motor Axes Drive Materials
 | Stepper motor | Nema 17 or 23 | https://www.amazon.com/Stepper-Bipolar-Connector-compatible-Printer/dp/B00PNEQKC0
 | GT2-3mm Motor pulley | 16 tooth
 | GT2-3mm Leadscrew pulley | 80-90 tooth
 | GT2-3mm 6mm wide belt | Design dependent
Optional
 | Buck Down Converter to 5V (Can be used instead of R-78C5.0-1.0)
 | 5V Power Supply (Can be used instead of R-78C5.0-1.0)
1 | Overhead drive motor for cutting frames |  | https://www.amazon.com/gp/product/B016EJ1WB6/ref=ppx_yo_dt_b_asin_title_o01_s00?ie=UTF8&psc=1 | https://www.sherline.com/product/33050-dc-motor-speed-control-units/
6 | Limit switches
 | MagSwitch 95 and/or 150 |  | https://www.amazon.com/Magswitch-MagJig-150-Set-2/dp/B01B59KW6Q | https://www.amazon.com/Magswitch-MAGJIG-95-MagJig-Yellow/dp/B003FWERRC
2 | 1/2"x1/8" Neodymium magnets for Nextion housing (if desired to hold to steel rose engine bed) |  | https://www.kjmagnetics.com/proddetail.asp?prod=D82

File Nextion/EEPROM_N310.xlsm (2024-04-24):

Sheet: Ini File
Ini_Sort | Page | Key | Value | EEProm | End | Position | Hex | ASCII | Char | Comments | Open | Used | 108 | 916 | 1024 | ;Ini file | Value | ;Ini file Fast | Value | ;Ini file Reset
1 |  | ; Rose Engine Ini file |  |  |  |  |  |  |  |  |  |  |  |  |  | ; Rose Engine Ini file |  | ; Rose Engine Ini file |  | ; Rose Engine Ini file
2 |  | ; V3.0 |  |  |  |  |  |  |  |  |  |  |  |  |  | ; V3.0 |  | ; Set higher speeds |  | ; Change all values to opposite of defaults
3 |  | [Preferences] |  |  |  |  |  |  |  |  |  |  | 108 | 916 |  | [Preferences] |  | [Preferences] |  | [Preferences]
4 |  | ; |  |  |  |  |  |  |  |  |  |  |  |  |  | ; |  | ; |  | ;
5 |  | ;More |  |  |  |  |  |  |  |  |  |  |  |  |  | ;More |  | ;More |  | ;More
6 | More | VendorId | 4 | 0 | 3 | 16 | F4 | 244 | ô |  | 0 | 0 |  |  |  | VendorId=4 | 4 | VendorId=4 | 3 | VendorId=3
7 | More | MotorCount | 5 | 0 | 3 | 24 | F5 | 245 | õ |  | 0 | 0 |  |  |  | MotorCount=5 | 5 | MotorCount=5 | 3 | MotorCount=3
8 |  | ;CutterMotorPin must be greater than 16 on 4 motor board. |  |  |  |  |  |  |  |  |  |  |  |  |  | ;CutterMotorPin must be greater than 16 on 4 motor board. |  | ;CutterMotorPin must be greater than 16 on 4 motor board. |  | ;CutterMotorPin must be greater than 16 on 4 motor board.
9 |  | ;CutterMotorPin must be greater than 24 on 5 motor board. |  |  |  |  |  |  |  |  |  |  |  |  |  | ;CutterMotorPin must be greater than 24 on 5 motor board. |  | ;CutterMotorPin must be greater than 24 on 5 motor board. |  | ;CutterMotorPin must be greater than 24 on 5 motor board.
10 | More | Auxillary Pin | 47 | 104 | 107 | 24 | AA | 170 | ª |  | 0 | 0 |  |  |  | Auxillary Pin=47 | 47 | Auxillary Pin=47 | 54 | Auxillary Pin=54
11 | More | KeepSteppersEnabled | 0 | 416 | 419 | 24 | 50 | 80 | P | 0-false | 0 | 0 |  |  |  | KeepSteppersEnabled=0 | 0 | KeepSteppersEnabled=0 | 1 | KeepSteppersEnabled=1
12 |  | ; Spindle |  |  |  |  |  |  |  |  |  |  |  |  |  | ; Spindle |  | ; Spindle |  | ; Spindle
13 | Spindle | Microsteps_Spindle | 32 | 200 | 203 |  | 70 | 112 | p |  | 0 | 4 |  |  |  | Microsteps_Spindle=32 | 32 | Microsteps_Spindle=32 | 16 | Microsteps_Spindle=16
14 | Spindle | StepsPer360_Spindle | 200 | 80 | 83 |  | 72 | 114 | r |  | 0 | 4 |  |  |  | StepsPer360_Spindle=200 | 200 | StepsPer360_Spindle=200 | 400 | StepsPer360_Spindle=400
15 | Spindle | GearRatio_Spindle | 9 | 268 | 275 |  | 73 | 115 | s |  | 0 | 8 |  |  |  | GearRatio_Spindle=9 | 1 | GearRatio_Spindle=1 | 1.111 | GearRatio_Spindle=1.111
16 | Spindle | ;Polarity: Low=1, High=0 |  |  |  |  |  |  |  |  |  |  |  |  |  | ;Polarity: Low=1, High=0 |  | ;Polarity: Low=1, High=0 |  | ;Polarity: Low=1, High=0
17 | Spindle | Polarity_Spindle | 1 | 460 | 463 | 16 | D8 | 216 | Ø |  | 0 | 0 |  |  |  | Polarity_Spindle=1 | 1 | Polarity_Spindle=1 | 0 | Polarity_Spindle=0
18 |  | ;Z Axis |  |  |  |  |  |  |  |  |  |  |  |  |  | ;Z Axis |  | ;Z Axis |  | ;Z Axis
19 | Z | Microsteps_Z | 32 | 196 | 199 |  | 79 | 121 | y |  | 0 | 4 |  |  |  | Microsteps_Z=32 | 32 | Microsteps_Z=32 | 8 | Microsteps_Z=8
20 | Z | StepsPer360_Z | 200 | 468 | 471 |  | 7A | 122 | z |  | 0 | 4 |  |  |  | StepsPer360_Z=200 | 200 | StepsPer360_Z=200 | 400 | StepsPer360_Z=400
21 | Z | DistancePer360_Z | 0.187 | 512 | 519 |  | 7B | 123 | { |  | 0 | 8 |  |  |  | DistancePer360_Z=0.187 | 0.01 | DistancePer360_Z=0.01 | 0.013654 | DistancePer360_Z=0.013654
22 | Z | Polarity_Z | 1 | 460 | 463 | 0 | D9 | 217 | Ù |  | 0 | 4 |  |  |  | Polarity_Z=1 | 1 | Polarity_Z=1 | 0 | Polarity_Z=0
23 |  | ; Hand: 0=Left, 1=Right |  |  |  |  |  |  |  |  |  |  |  |  |  | ; Hand: 0=Left, 1=Right |  | ; Hand: 0=Left, 1=Right |  | ; Hand: 0=Left, 1=Right
24 | Z | Leadscrew_Hand_Z | 0 | 252 | 255 | 0 |  |  |  |  | 0 | 4 |  |  |  | Leadscrew_Hand_Z=0 | 1 | Leadscrew_Hand_Z=1 | 0 | Leadscrew_Hand_Z=0
25 |  | ;X Axis |  |  |  |  |  |  |  |  |  |  |  |  |  | ;X Axis |  | ;X Axis |  | ;X Axis
26 | X | XorAltXSelected | 0 | 188 | 191 |  | F3 | 243 | ó |  | 0 | 4 |  |  |  | XorAltXSelected=0 | 0 | XorAltXSelected=0 | 1 | XorAltXSelected=1
27 | X | Microsteps_X | 32 | 564 | 567 |  | BB | 187 | » |  | 0 | 4 |  |  |  | Microsteps_X=32 | 32 | Microsteps_X=32 | 16 | Microsteps_X=16
28 | X | StepsPer360_X | 200 | 484 | 487 |  | BC | 188 | ¼ |  | 0 | 4 |  |  |  | StepsPer360_X=200 | 200 | StepsPer360_X=200 | 400 | StepsPer360_X=400
29 | X | DistancePer360_X | 0.187 | 488 | 495 |  | BD | 189 | ½ |  | 0 | 8 |  |  |  | DistancePer360_X=0.187 | 0.01 | DistancePer360_X=0.01 | 1.02 | DistancePer360_X=1.02
30 | X | Polarity_X | 1 | 176 | 179 | 16 | DA | 218 | Ú |  | 0 | 0 |  |  |  | Polarity_X=1 | 1 | Polarity_X=1 | 0 | Polarity_X=0
31 | X | Leadscrew_Hand_X | 0 | 252 | 255 | 8 |  |  |  |  | 0 | 0 |  |  |  | Leadscrew_Hand_X=0 | 1 | Leadscrew_Hand_X=1 | 0 | Leadscrew_Hand_X=0
32 |  | ;Alternate X Axis |  |  |  |  |  |  |  |  |  |  |  |  |  | ;Alternate X Axis |  | ;Alternate X Axis |  | ;Alternate X Axis
33 | AltX | Microsteps_AltX | 32 | 568 | 571 |  | EF | 239 | ï |  | 0 | 4 |  |  |  | Microsteps_AltX=32 | 32 | Microsteps_AltX=32 | 8 | Microsteps_AltX=8
34 | AltX | StepsPer360_AltX | 200 | 204 | 207 |  | F0 | 240 | ð |  | 0 | 4 |  |  |  | StepsPer360_AltX=200 | 200 | StepsPer360_AltX=200 | 100 | StepsPer360_AltX=100
35 | AltX | DistancePer360_AltX | 0.283 | 216 | 223 |  | 4F | 79 | O |  | 0 | 8 |  |  |  | DistancePer360_AltX=0.283 | 0.01 | DistancePer360_AltX=0.01 | 36 | DistancePer360_AltX=36
36 | AltX | Polarity_AltX | 1 | 176 | 179 | 0 | F2 | 242 | ò |  | 0 | 4 |  |  |  | Polarity_AltX=1 | 1 | Polarity_AltX=1 | 0 | Polarity_AltX=0
37 | AltX | Leadscrew_Hand_AltX | 1 | 252 | 255 | 16 |  |  |  |  | 0 | 0 |  |  |  | Leadscrew_Hand_AltX=1 | 1 | Leadscrew_Hand_AltX=1 | 0 | Leadscrew_Hand_AltX=0
38 |  | ;M3 Axis |  |  |  |  |  |  |  |  |  |  |  |  |  | ;M3 Axis |  | ;M3 Axis |  | ;M3 Axis
39 | M3 | Microsteps_M3 | 32 | 92 | 95 |  | 76 | 118 | v |  | 0 | 4 |  |  |  | Microsteps_M3=32 | 32 | Microsteps_M3=32 | 8 | Microsteps_M3=8
40 | M3 | StepsPer360_M3 | 200 | 544 | 547 |  | 77 | 119 | w |  | 0 | 4 |  |  |  | StepsPer360_M3=200 | 200 | StepsPer360_M3=200 | 600 | StepsPer360_M3=600
41 | M3 | GearRatio_M3 | 30 | 548 | 555 |  | 78 | 120 | x |  | 0 | 8 |  |  |  | GearRatio_M3=30 | 1 | GearRatio_M3=1 | 34 | GearRatio_M3=34
42 | M3 | Polarity_M3 | 1 | 416 | 419 | 0 | DB | 219 | Û | 1-Low | 0 | 4 |  |  |  | Polarity_M3=1 | 1 | Polarity_M3=1 | 0 | Polarity_M3=0
43 | M3 | DistancePer360_M3 | 1.02354 | 408 | 415 |  | 74 | 116 | t |  | 0 | 8 |  |  |  | DistancePer360_M3=1.02354 | 0.01 | DistancePer360_M3=0.01 | 12 | DistancePer360_M3=12
44 | M3 | RadialOrLineal_M3 | 0 | 416 | 419 | 16 | C3 | 195 | Ã | 0-Radial | 0 | 0 |  |  |  | RadialOrLineal_M3=0 | 0 | RadialOrLineal_M3=0 | 1 | RadialOrLineal_M3=1
45 | M3 | M3Radius | 5.124 | 688 | 695 |  | FE | 254 | þ |  | 0 | 8 |  |  |  | M3Radius=5.124 | 5 | M3Radius=5 | 65 | M3Radius=65
46 | M3 | Leadscrew_Hand_M3 | 1 | 252 | 255 | 24 |  |  |  |  | 0 | 0 |  |  |  | Leadscrew_Hand_M3=1 | 1 | Leadscrew_Hand_M3=1 | 0 | Leadscrew_Hand_M3=0
47 |  | ;M4 Axis |  |  |  |  |  |  |  |  |  |  |  |  |  | ;M4 Axis |  | ;M4 Axis |  | ;M4 Axis
48 | M4 | Microsteps_M4 | 32 | 96 | 99 |  | 71 | 113 | q |  | 0 | 4 |  |  |  | Microsteps_M4=32 | 32 | Microsteps_M4=32 | 2 | Microsteps_M4=2
49 | M4 | StepsPer360_M4 | 200 | 404 | 407 |  | A7 | 167 | § |  | 0 | 4 |  |  |  | StepsPer360_M4=200 | 200 | StepsPer360_M4=200 | 300 | StepsPer360_M4=300
50 | M4 | GearRatio_M4 | 30 | 380 | 387 |  | A9 | 169 | © |  | 0 | 8 |  |  |  | GearRatio_M4=30 | 30 | GearRatio_M4=30 | 12 | GearRatio_M4=12
51 | M4 | Polarity_M4 | 1 | 460 | 463 | 24 | 75 | 117 | u |  | 0 | 0 |  |  |  | Polarity_M4=1 | 1 | Polarity_M4=1 | 0 | Polarity_M4=0
52 | M4 | DistancePer360_M4 | 0.0254 | 600 | 607 |  | A8 | 168 | ¨ |  | 0 | 8 |  |  |  | DistancePer360_M4=0.0254 | 0.01 | DistancePer360_M4=0.01 | 45 | DistancePer360_M4=45
53 | M4 | RadialOrLineal_M4 | 1 | 460 | 463 | 8 | A2 | 162 | ¢ |  | 0 | 0 |  |  |  | RadialOrLineal_M4=1 | 1 | RadialOrLineal_M4=1 | 0 | RadialOrLineal_M4=0
54 | M4 | M4Radius | 11.258 | 664 | 671 |  | B0 | 176 | ° |  | 0 | 8 |  |  |  | M4Radius=11.258 | 5 | M4Radius=5 | 1 | M4Radius=1
55 | M4 | Leadscrew_Hand_M4 | 1 | 264 | 267 |  |  |  |  |  | 0 | 4 |  |  |  | Leadscrew_Hand_M4=1 | 1 | Leadscrew_Hand_M4=1 | 0 | Leadscrew_Hand_M4=0
56 |  | ; |  |  |  |  |  |  |  |  |  |  |  |  |  | ; |  | ; |  | ;
57 |  | [Limits] |  |  |  |  |  |  |  |  |  |  |  |  |  | [Limits] |  | [Limits] |  | [Limits]
58 |  | ; |  |  |  |  |  |  |  |  |  |  |  |  |  | ; |  | ; |  | ;
59 |  | ;Limit Switches and Stop pins must be greater than 16 on 4 motor board. |  |  |  |  |  |  |  |  |  |  |  |  |  | ;Limit Switches and Stop pins must be greater than 16 on 4 motor board. |  | ;Limit Switches and Stop pins must be greater than 16 on 4 motor board. |  | ;Limit Switches and Stop pins must be greater than 16 on 4 motor board.
60 |  | ;Limit Switches and Stop pins must be greater than 24 on 5 motor board. |  |  |  |  |  |  |  |  |  |  |  |  |  | ;Limit Switches and Stop pins must be greater than 24 on 5 motor board. |  | ;Limit Switches and Stop pins must be greater than 24 on 5 motor board. |  | ;Limit Switches and Stop pins must be greater than 24 on 5 motor board.
61 | Limits | Min_Z | 24 | 424 | 427 | 8 | DC | 220 | Ü |  | 0 | 0 |  |  |  | Min_Z=24 | 24 | Min_Z=24 | 31 | Min_Z=31
62 | Limits | Max_Z | 26 | 424 | 427 | 0 | DD | 221 | Ý |  | 0 | 4 |  |  |  | Max_Z=26 | 26 | Max_Z=26 | 31 | Max_Z=31
63 | Limits | Min_X | 24 | 424 | 427 | 16 | DE | 222 | Þ |  | 0 | 0 |  |  |  | Min_X=24 | 24 | Min_X=24 | 31 | Min_X=31
64 | Limits | Max_X | 26 | 424 | 427 | 24 | DF | 223 | ß |  | 0 | 0 |  |  |  | Max_X=26 | 26 | Max_X=26 | 31 | Max_X=31
65 | Limits | Min_M3 | 24 | 576 | 579 | 0 | E0 | 224 | à |  | 0 | 4 |  |  |  | Min_M3=24 | 24 | Min_M3=24 | 31 | Min_M3=31
66 | Limits | Max_M3 | 26 | 576 | 579 | 8 | E1 | 225 | á |  | 0 | 0 |  |  |  | Max_M3=26 | 26 | Max_M3=26 | 31 | Max_M3=31
67 | Limits | Min_M4 | 24 | 368 | 371 | 0 | AF | 175 | ¯ |  | 0 | 4 |  |  |  | Min_M4=24 | 24 | Min_M4=24 | 31 | Min_M4=31
68 | Limits | Max_M4 | 26 | 368 | 371 | 8 | AE | 174 | ® |  | 0 | 0 |  |  |  | Max_M4=26 | 26 | Max_M4=26 | 31 | Max_M4=31
69 |  | ;Stop spindle when limit hit = 0. Leave spindle running =1 |  |  |  |  |  |  |  |  |  |  |  |  |  | ;Stop spindle when limit hit = 0. Leave spindle running =1 |  | ;Stop spindle when limit hit = 0. Leave spindle running =1 |  | ;Stop spindle when limit hit = 0. Leave spindle running =1
70 | Limits | StopSpindle | 0 | 576 | 579 | 24 | 56 | 86 | V |  | 0 | 0 |  |  |  | StopSpindle=0 | 1 | StopSpindle=1 | 1 | StopSpindle=1
71 | Limits | Stop | 28 | 576 | 579 | 16 | 47 | 71 | G |  | 0 | 0 |  |  |  | Stop=28 | 28 | Stop=28 | 31 | Stop=31
72 |  | ;Normally Closed=0, Normally Open=1 |  |  |  |  |  |  |  |  |  |  |  |  |  | ;Normally Closed=0, Normally Open=1 |  | ;Normally Closed=0, Normally Open=1 |  | ;Normally Closed=0, Normally Open=1
73 | Limits | NC-NO | 1 | 416 | 419 | 8 | A1 | 161 | ¡ | 1 - NO | 0 | 0 |  |  |  | NC-NO=1 | 1 | NC-NO=1 | 0 | NC-NO=0
74 |  | ; |  |  |  |  |  |  |  |  |  |  |  |  |  | ; |  | ; |  | ;
75 |  | [Returns] |  |  |  |  |  |  |  |  |  |  |  |  |  | [Returns] |  | [Returns] |  | [Returns]
76 |  | ; |  |  |  |  |  |  |  |  |  |  |  |  |  | ; |  | ; |  | ;
77 |  | ;Return |  |  |  |  |  |  |  |  |  |  |  |  |  | ;Return |  | ;Return |  | ;Return
78 |  | ; All speeds and accellerations are in steps per second |  |  |  |  |  |  |  |  |  |  |  |  |  | ; All speeds and accellerations are in steps per second |  | ; All speeds and accellerations are in steps per second |  | ; All speeds and accellerations are in steps per second
79 | Returns | MaxSpeed_Spindle | 30000 | 808 | 811 |  | E8 | 232 | è |  | 0 | 4 |  |  |  | MaxSpeed_Spindle=30000 | 15001 | MaxSpeed_Spindle=15001 | 1001 | MaxSpeed_Spindle=1001
80 | Returns | Accel_Spindle | 20000 | 812 | 815 |  | E9 | 233 | é |  | 0 | 4 |  |  |  | Accel_Spindle=20000 | 15002 | Accel_Spindle=15002 | 1002 | Accel_Spindle=1002
81 | Returns | MaxSpeed_Axis_Z | 30000 | 816 | 819 |  | EA | 234 | ê |  | 0 | 4 |  |  |  | MaxSpeed_Axis_Z=30000 | 15003 | MaxSpeed_Axis_Z=15003 | 1003 | MaxSpeed_Axis_Z=1003
82 | Returns | Accel_Axis_Z | 20000 | 772 | 775 |  | EB | 235 | ë |  | 0 | 4 |  |  |  | Accel_Axis_Z=20000 | 15000 | Accel_Axis_Z=15000 | 1000 | Accel_Axis_Z=1000
83 | Returns | MaxSpeed_Axis_X | 30000 | 784 | 787 |  | EA | 234 | ê |  | 0 | 4 |  |  |  | MaxSpeed_Axis_X=30000 | 30000 | MaxSpeed_Axis_X=30000 | 1000 | MaxSpeed_Axis_X=1000
84 | Returns | Accel_Axis_X | 20000 | 788 | 791 |  | EB | 235 | ë |  | 0 | 4 |  |  |  | Accel_Axis_X=20000 | 15000 | Accel_Axis_X=15000 | 1000 | Accel_Axis_X=1000
85 | Returns | MaxSpeed_Axis_M3 | 30000 | 776 | 779 |  | EA | 234 | ê |  | 0 | 4 |  |  |  | MaxSpeed_Axis_M3=30000 | 30000 | MaxSpeed_Axis_M3=30000 | 1000 | MaxSpeed_Axis_M3=1000
86 | Returns | Accel_Axis_M3 | 20000 | 780 | 783 |  | EB | 235 | ë |  | 0 | 4 |  |  |  | Accel_Axis_M3=20000 | 15000 | Accel_Axis_M3=15000 | 1000 | Accel_Axis_M3=1000
87 | Returns | MaxSpeed_Axis_M4 | 30000 | 856 | 859 |  | EA | 234 | ê |  | 0 | 4 |  |  |  | MaxSpeed_Axis_M4=30000 | 15004 | MaxSpeed_Axis_M4=15004 | 1004 | MaxSpeed_Axis_M4=1004
88 | Returns | Accel_Axis_M4 | 20000 | 860 | 863 |  | EB | 235 | ë |  | 0 | 4 |  |  |  | Accel_Axis_M4=20000 | 15005 | Accel_Axis_M4=15005 | 1005 | Accel_Axis_M4=1005
89 |  | ; |  |  |  |  |  |  |  |  |  |  |  |  |  | ; |  | ; |  | ;
90 |  | [Main] |  |  |  |  |  |  |  |  |  |  |  |  |  | [Main] |  | [Main] |  | [Main]
91 |  | ; |  |  |  |  |  |  |  |  |  |  |  |  |  | ; |  | ; |  | ;
92 |  | ;Axis Ids: |  |  |  |  |  |  |  |  |  |  |  |  |  | ;Axis Ids: |  | ;Axis Ids: |  | ;Axis Ids:
93 |  | ;----------------- |  |  |  |  |  |  |  |  |  |  |  |  |  | ;----------------- |  | ;----------------- |  | ;-----------------
94 |  | ;Z=1 |  |  |  |  |  |  |  |  |  |  |  |  |  | ;Z=1 |  | ;Z=1 |  | ;Z=1
95 |  | ;X=2 |  |  |  |  |  |  |  |  |  |  |  |  |  | ;X=2 |  | ;X=2 |  | ;X=2
96 |  | ;M3=3 |  |  |  |  |  |  |  |  |  |  |  |  |  | ;M3=3 |  | ;M3=3 |  | ;M3=3
97 |  | ;M4=4 |  |  |  |  |  |  |  |  |  |  |  |  |  | ;M4=4 |  | ;M4=4 |  | ;M4=4
98 |  | ;Spindle=0 |  |  |  |  |  |  |  |  |  |  |  |  |  | ;Spindle=0 |  | ;Spindle=0 |  | ;Spindle=0
99 |  | ;----------------- |  |  |  |  |  |  |  |  |  |  |  |  |  | ;----------------- |  | ;----------------- |  | ;-----------------
100 | Main | AxisId | 1 | 0 | 3 | 8 | 42 | 66 | B |  | 0 | 0 |  |  |  | AxisId=1 | 2 | AxisId=2 | 3 | AxisId=3
101 |  | ;Spindle |  |  |  |  |  |  |  |  |  |  |  |  |  | ;Spindle |  | ;Spindle |  | ;Spindle
102 | Main | MaxSpeed_Spindle | 15000 | 872 | 875 |  | 3A | 58 | : |  | 0 | 4 |  |  |  | MaxSpeed_Spindle=15000 | 30000 | MaxSpeed_Spindle=30000 | 1000 | MaxSpeed_Spindle=1000
103 | Main | Accel_Spindle | 20000 | 912 | 915 |  | 3B | 59 | ; |  | 0 | 4 |  |  |  | Accel_Spindle=20000 | 15000 | Accel_Spindle=15000 | 1000 | Accel_Spindle=1000
104 | Main | SpeedPercentage_Spindle | 51 | 0 | 3 | 0 | 6E | 110 | n |  | 0 | 4 |  |  |  | SpeedPercentage_Spindle=51 | 100 | SpeedPercentage_Spindle=100 | 11 | SpeedPercentage_Spindle=11
105 |  | ;Z Axis |  |  |  |  |  |  |  |  |  |  |  |  |  | ;Z Axis |  | ;Z Axis |  | ;Z Axis
106 | Main | MaxSpeed_Z | 15000 | 952 | 955 |  | B9 | 185 | ¹ |  | 0 | 4 |  |  |  | MaxSpeed_Z=15000 | 30000 | MaxSpeed_Z=30000 | 1000 | MaxSpeed_Z=1000
107 | Main | Accel_Z | 20000 | 972 | 975 |  | BA | 186 | º |  | 0 | 4 |  |  |  | Accel_Z=20000 | 15000 | Accel_Z=15000 | 1000 | Accel_Z=1000
108 | Main | SpeedPercentage_Z | 53 | 8 | 11 | 0 | 6F | 111 | o |  | 0 | 4 |  |  |  | SpeedPercentage_Z=53 | 100 | SpeedPercentage_Z=100 | 11 | SpeedPercentage_Z=11
109 |  | ;X Axis |  |  |  |  |  |  |  |  |  |  |  |  |  | ;X Axis |  | ;X Axis |  | ;X Axis
110 | Main | MaxSpeed_X | 4000 | 992 | 995 |  | B9 | 185 | ¹ |  | 0 | 4 |  |  |  | MaxSpeed_X=4000 | 30000 | MaxSpeed_X=30000 | 1000 | MaxSpeed_X=1000
111 | Main | Accel_X | 20000 | 1004 | 1007 |  | BA | 186 | º |  | 0 | 4 |  |  |  | Accel_X=20000 | 15000 | Accel_X=15000 | 1000 | Accel_X=1000
112 | Main | SpeedPercentage_X | 54 | 8 | 11 | 8 | 6F | 111 | o |  | 0 | 0 |  |  |  | SpeedPercentage_X=54 | 100 | SpeedPercentage_X=100 | 11 | SpeedPercentage_X=11
113 |  | ;M3 Axis |  |  |  |  |  |  |  |  |  |  |  |  |  | ;M3 Axis |  | ;M3 Axis |  | ;M3 Axis
114 | Main | MaxSpeed_M3 | 5007 | 1016 | 1019 |  | B9 | 185 | ¹ |  | 0 | 4 |  |  |  | MaxSpeed_M3 =5007 | 30000 | MaxSpeed_M3 =30000 | 10001 | MaxSpeed_M3 =10001
115 | Main | Accel_M3 | 20000 | 1020 | 1023 |  | BA | 186 | º |  | 0 | 4 |  |  |  | Accel_M3 =20000 | 15000 | Accel_M3 =15000 | 1000 | Accel_M3 =1000
116 | Main | SpeedPercentage_M3 | 59 | 8 | 11 | 16 | 6F | 111 | o |  | 0 | 0 |  |  |  | SpeedPercentage_M3 =59 | 100 | SpeedPercentage_M3 =100 | 10 | SpeedPercentage_M3 =10
117 |  | ;M4 Axis |  |  |  |  |  |  |  |  |  |  |  |  |  | ;M4 Axis |  | ;M4 Axis |  | ;M4 Axis
118 | Main | MaxSpeed_M4 | 5007 | 916 | 919 |  | B9 | 185 | ¹ |  | 0 | 4 |  |  |  | MaxSpeed_M4 =5007 | 30000 | MaxSpeed_M4 =30000 | 1000 | MaxSpeed_M4 =1000
119 | Main | Accel_M4 | 20000 | 920 | 923 |  | BA | 186 | º |  | 0 | 4 |  |  |  | Accel_M4 =20000 | 15000 | Accel_M4 =15000 | 1000 | Accel_M4 =1000
120 | Main | SpeedPercentage_M4 | 60 | 8 | 11 | 24 | 6F | 111 | o |  | 0 | 0 |  |  |  | SpeedPercentage_M4 =60 | 100 | SpeedPercentage_M4 =100 | 11 | SpeedPercentage_M4 =11
121 |  | ; |  |  |  |  |  |  |  |  |  |  |  |  |  | ; |  | ; |  | ;
122 |  | [One_Multi] |  |  |  |  |  |  |  |  |  |  |  |  |  | [One_Multi] |  | [One_Multi] |  | [One_Multi]
123 |  | ; |  |  |  |  |  |  |  |  |  |  |  |  |  | ; |  | ; |  | ;
124 |  | ; Settings are shared between One and Multi pages. |  |  |  |  |  |  |  |  |  |  |  |  |  | ; Settings are shared between One and Multi pages. |  | ; Settings are shared between One and Multi pages. |  | ; Settings are shared between One and Multi pages.
125 | Multi | AxisId | 1 | 88 | 91 | 8 | 42 | 66 | B |  | 0 | 0 |  |  |  | AxisId=1 | 1 | AxisId=1 | 3 | AxisId=3
126 |  | ; MultiAxesRun and Direction values are ANDed together. |  |  |  |  |  |  |  |  |  |  |  |  |  | ; MultiAxesRun and Direction values are ANDed together. |  | ; MultiAxesRun and Direction values are ANDed together. |  | ; MultiAxesRun and Direction values are ANDed together.
127 | Multi | MultiAxesIDs | 0 | 88 | 91 | 16 | C8 | 200 | È | Values ANDed together (1,2,4,8,16) | 0 | 0 |  |  |  | MultiAxesIDs=0 | 0 | MultiAxesIDs=0 | 2 | MultiAxesIDs=2
128 |  | ;Spindle |  |  |  |  |  |  |  |  |  |  |  |  |  | ;Spindle |  | ;Spindle |  | ;Spindle
129 | Multi | MaxSpeed_Spindle | 2500 | 928 | 931 |  | 3A | 58 | : |  | 0 | 4 |  |  |  | MaxSpeed_Spindle=2500 | 10 | MaxSpeed_Spindle=10 | 9 | MaxSpeed_Spindle=9
130 | Multi | Accel_Spindle | 20000 | 940 | 943 |  | 3B | 59 | ; |  | 0 | 4 |  |  |  | Accel_Spindle=20000 | 10 | Accel_Spindle=10 | 9 | Accel_Spindle=9
131 | Multi | SpeedPercentage_Spindle | 61 | 88 | 91 | 0 | 6E | 110 | n |  | 0 | 4 |  |  |  | SpeedPercentage_Spindle=61 | 100 | SpeedPercentage_Spindle=100 | 11 | SpeedPercentage_Spindle=11
132 | Multi | TargetDistance_Spindle | 39.45 | 388 | 395 |  | 7E | 126 | ~ |  | 0 | 8 |  |  |  | TargetDistance_Spindle=39.45 | 360 | TargetDistance_Spindle=360 | 11 | TargetDistance_Spindle=11
133 |  | ; CW=2, CCW=3 |  |  |  |  |  |  |  |  |  |  |  |  |  | ; CW=2, CCW=3 |  | ; CW=2, CCW=3 |  | ; CW=2, CCW=3
134 | Multi | Direction_Spindle | 2 | 712 | 715 |  | C2 | 194 | Â |  | 0 | 4 |  |  |  | Direction_Spindle=2 | 2 | Direction_Spindle=2 | 3 | Direction_Spindle=3
135 |  | ;Z Axis |  |  |  |  |  |  |  |  |  |  |  |  |  | ;Z Axis |  | ;Z Axis |  | ;Z Axis
136 | Multi | MaxSpeed_Z | 5062 | 852 | 855 |  | B9 | 185 | ¹ |  | 0 | 4 |  |  |  | MaxSpeed_Z=5062 | 6 | MaxSpeed_Z=6 | 5 | MaxSpeed_Z=5
137 | Multi | Accel_Z | 20000 | 768 | 771 |  | BA | 186 | º |  | 0 | 4 |  |  |  | Accel_Z=20000 | 30000 | Accel_Z=30000 | 1000 | Accel_Z=1000
138 | Multi | SpeedPercentage_Z | 64 | 76 | 79 | 0 | 6F | 111 | o |  | 0 | 4 |  |  |  | SpeedPercentage_Z=64 | 100 | SpeedPercentage_Z=100 | 11 | SpeedPercentage_Z=11
139 | Multi | TargetDistance_Z | 2.123 | 652 | 659 |  | 67 | 103 | g |  | 0 | 8 |  |  |  | TargetDistance_Z=2.123 | 0.2 | TargetDistance_Z=0.2 | 11 | TargetDistance_Z=11
140 |  | ; Right=2, Left=3 |  |  |  |  |  |  |  |  |  |  |  |  |  | ; Right=2, Left=3 |  | ; Right=2, Left=3 |  | ; Right=2, Left=3
141 | Multi | Direction_Z | 2 | 716 | 719 |  | C2 | 194 | Â |  | 0 | 4 |  |  |  | Direction_Z=2 | 2 | Direction_Z=2 | 3 | Direction_Z=3
142 |  | ;X Axis |  |  |  |  |  |  |  |  |  |  |  |  |  | ;X Axis |  | ;X Axis |  | ;X Axis
143 | Multi | MaxSpeed_X | 5065 | 848 | 851 |  | B9 | 185 | ¹ |  | 0 | 4 |  |  |  | MaxSpeed_X=5065 | 5 | MaxSpeed_X=5 | 4 | MaxSpeed_X=4
144 | Multi | Accel_X | 20000 | 908 | 911 |  | BA | 186 | º |  | 0 | 4 |  |  |  | Accel_X=20000 | 8 | Accel_X=8 | 7 | Accel_X=7
145 | Multi | SpeedPercentage_X | 67 | 76 | 79 | 8 | 6F | 111 | o |  | 0 | 0 |  |  |  | SpeedPercentage_X=67 | 100 | SpeedPercentage_X=100 | 11 | SpeedPercentage_X=11
146 | Multi | TargetDistance_X | 3.514 | 140 | 147 |  | 68 | 104 | h |  | 0 | 8 |  |  |  | TargetDistance_X=3.514 | 0.2 | TargetDistance_X=0.2 | 11 | TargetDistance_X=11
147 |  | ; Right=2, Left=3 |  |  |  |  |  |  |  |  |  |  |  |  |  | ; Right=2, Left=3 |  | ; Right=2, Left=3 |  | ; Right=2, Left=3
148 | Multi | Direction_X | 3 | 720 | 723 |  | C2 | 194 | Â |  | 0 | 4 |  |  |  | Direction_X=3 | 3 | Direction_X=3 | 2 | Direction_X=2
149 |  | ;M3 Axis |  |  |  |  |  |  |  |  |  |  |  |  |  | ;M3 Axis |  | ;M3 Axis |  | ;M3 Axis
150 | Multi | MaxSpeed_M3 | 5068 | 864 | 867 |  | B9 | 185 | ¹ |  | 0 | 4 |  |  |  | MaxSpeed_M3=5068 | 7 | MaxSpeed_M3=7 | 6 | MaxSpeed_M3=6
151 | Multi | Accel_M3 | 20000 | 932 | 935 |  | BA | 186 | º |  | 0 | 4 |  |  |  | Accel_M3=20000 | 11 | Accel_M3=11 | 10 | Accel_M3=10
152 | Multi | SpeedPercentage_M3 | 70 | 76 | 79 | 16 | 6F | 111 | o |  | 0 | 0 |  |  |  | SpeedPercentage_M3=70 | 100 | SpeedPercentage_M3=100 | 11 | SpeedPercentage_M3=11
153 | Multi | TargetDistance_M3 | 1.369 | 244 | 251 |  | 6A | 106 | j |  | 0 | 8 |  |  |  | TargetDistance_M3=1.369 | 360 | TargetDistance_M3=360 | 11 | TargetDistance_M3=11
154 |  | ; Right and CW=2, Left and CCW=3 |  |  |  |  |  |  |  |  |  |  |  |  |  | ; Right and CW=2, Left and CCW=3 |  | ; Right and CW=2, Left and CCW=3 |  | ; Right and CW=2, Left and CCW=3
155 | Multi | Direction_M3 | 2 | 724 | 727 |  | C2 | 194 | Â |  | 0 | 4 |  |  |  | Direction_M3=2 | 2 | Direction_M3=2 | 3 | Direction_M3=3
156 |  | ;M4 Axis |  |  |  |  |  |  |  |  |  |  |  |  |  | ;M4 Axis |  | ;M4 Axis |  | ;M4 Axis
157 | Multi | MaxSpeed_M4 | 5068 | 836 | 839 |  | B9 | 185 | ¹ |  | 0 | 4 |  |  |  | MaxSpeed_M4=5068 | 4 | MaxSpeed_M4=4 | 3 | MaxSpeed_M4=3
158 | Multi | Accel_M4 | 20000 | 924 | 927 |  | BA | 186 | º |  | 0 | 4 |  |  |  | Accel_M4=20000 | 9 | Accel_M4=9 | 8 | Accel_M4=8
159 | Multi | SpeedPercentage_M4 | 70 | 76 | 79 | 24 | 6F | 111 | o |  | 0 | 0 |  |  |  | SpeedPercentage_M4=70 | 100 | SpeedPercentage_M4=100 | 11 | SpeedPercentage_M4=11
160 | Multi | TargetDistance_M4 | 0.478 | 256 | 263 |  | C7 | 199 | Ç |  | 0 | 8 |  |  |  | TargetDistance_M4=0.478 | 0.02 | TargetDistance_M4=0.02 | 11 | TargetDistance_M4=11
161 |  | ; Right and CW=2, Left and CCW=3 |  |  |  |  |  |  |  |  |  |  |  |  |  | ; Right and CW=2, Left and CCW=3 |  | ; Right and CW=2, Left and CCW=3 |  | ; Right and CW=2, Left and CCW=3
162 | Multi | Direction_M4 | 3 | 728 | 731 |  | C2 | 194 | Â |  | 0 | 4 |  |  |  | Direction_M4=3 | 3 | Direction_M4=3 | 2 | Direction_M4=2
163 |  | ; |  |  |  |  |  |  |  |  |  |  |  |  |  | ; |  | ; |  | ;
164 |  | [Index] |  |  |  |  |  |  |  |  |  |  |  |  |  | [Index] |  | [Index] |  | [Index]
165 |  | ; |  |  |  |  |  |  |  |  |  |  |  |  |  | ; |  | ; |  | ;
166 |  | ;Axis Ids: |  |  |  |  |  |  |  |  |  |  |  |  |  | ;Axis Ids: |  | ;Axis Ids: |  | ;Axis Ids:
167 |  | ;----------------- |  |  |  |  |  |  |  |  |  |  |  |  |  | ;----------------- |  | ;----------------- |  | ;-----------------
168 |  | ;M3=3 |  |  |  |  |  |  |  |  |  |  |  |  |  | ;M3=3 |  | ;M3=3 |  | ;M3=3
169 |  | ;M4=4 |  |  |  |  |  |  |  |  |  |  |  |  |  | ;M4=4 |  | ;M4=4 |  | ;M4=4
170 |  | ;Spindle=0 |  |  |  |  |  |  |  |  |  |  |  |  |  | ;Spindle=0 |  | ;Spindle=0 |  | ;Spindle=0
171 |  | ;----------------- |  |  |  |  |  |  |  |  |  |  |  |  |  | ;----------------- |  | ;----------------- |  | ;-----------------
172 | Index | AxisId | 0 | 104 | 107 | 8 | 42 | 66 | B |  | 0 | 0 |  |  |  | AxisId=0 | 0 | AxisId=0 | 3 | AxisId=3
173 | Index | IndexId | 1 | 104 | 107 | 16 | F6 | 246 | ö |  | 0 | 0 |  |  |  | IndexId=1 | 1 | IndexId=1 | 3 | IndexId=3
174 |  | ; Spindle |  |  |  |  |  |  |  |  |  |  |  |  |  | ; Spindle |  | ; Spindle |  | ; Spindle
175 | Index | MaxSpeed_Spindle | 5070 | 904 | 907 |  | 3A | 58 | : |  | 0 | 4 |  |  |  | MaxSpeed_Spindle=5070 | 30000 | MaxSpeed_Spindle=30000 | 1000 | MaxSpeed_Spindle=1000
176 | Index | Accel_Spindle | 20000 | 944 | 947 |  | 3B | 59 | ; |  | 0 | 4 |  |  |  | Accel_Spindle=20000 | 20000 | Accel_Spindle=20000 | 1000 | Accel_Spindle=1000
177 | Index | SpeedPercentage_Spindle | 72 | 104 | 107 | 0 | 6E | 110 | n |  | 0 | 4 |  |  |  | SpeedPercentage_Spindle=72 | 100 | SpeedPercentage_Spindle=100 | 11 | SpeedPercentage_Spindle=11
178 |  | ; M3 |  |  |  |  |  |  |  |  |  |  |  |  |  | ; M3 |  | ; M3 |  | ; M3
179 | Index | MaxSpeed_M3 | 5072 | 804 | 807 |  | B9 | 185 | ¹ |  | 0 | 4 |  |  |  | MaxSpeed_M3=5072 | 2 | MaxSpeed_M3=2 | 3 | MaxSpeed_M3=3
180 | Index | Accel_M3 | 20000 | 956 | 959 |  | BA | 186 | º |  | 0 | 4 |  |  |  | Accel_M3=20000 | 20001 | Accel_M3=20001 | 1001 | Accel_M3=1001
181 | Index | SpeedPercentage_M3 | 73 | 368 | 371 | 16 | 6F | 111 | o |  | 0 | 0 |  |  |  | SpeedPercentage_M3=73 | 100 | SpeedPercentage_M3=100 | 11 | SpeedPercentage_M3=11
182 |  | ; M4 |  |  |  |  |  |  |  |  |  |  |  |  |  | ; M4 |  | ; M4 |  | ; M4
183 | Index | MaxSpeed_M4 | 5072 | 792 | 795 |  | B9 | 185 | ¹ |  | 0 | 4 |  |  |  | MaxSpeed_M4=5072 | 1 | MaxSpeed_M4=1 | 2 | MaxSpeed_M4=2
184 | Index | Accel_M4 | 20000 | 984 | 987 |  | BA | 186 | º |  | 0 | 4 |  |  |  | Accel_M4=20000 | 20002 | Accel_M4=20002 | 1002 | Accel_M4=1002
185 | Index | SpeedPercentage_M4 | 85 | 368 | 371 | 24 | 6F | 111 | o |  | 0 | 0 |  |  |  | SpeedPercentage_M4=85 | 100 | SpeedPercentage_M4=100 | 11 | SpeedPercentage_M4=11
186 |  | ;----------------- |  |  |  |  |  |  |  |  |  |  |  |  |  | ;----------------- |  | ;----------------- |  | ;-----------------
187 |  | ;Division:0 Degrees:1 |  |  |  |  |  |  |  |  |  |  |  |  |  | ;Division:0 Degrees:1 |  | ;Division:0 Degrees:1 |  | ;Division:0 Degrees:1
188 |  | ;Fixed:0 File:1 |  |  |  |  |  |  |  |  |  |  |  |  |  | ;Fixed:0 File:1 |  | ;Fixed:0 File:1 |  | ;Fixed:0 File:1
189 |  | ;----------------- |  |  |  |  |  |  |  |  |  |  |  |  |  | ;----------------- |  | ;----------------- |  | ;-----------------
190 |  | ;Index 1 |  |  |  |  |  |  |  |  |  |  |  |  |  | ;Index 1 |  | ;Index 1 |  | ;Index 1
191 | Index | DivisionsOrDegrees_1 | 1 | 192 | 195 |  | 45 | 69 | E |  | 0 | 4 |  |  |  | DivisionsOrDegrees_1=1 | 1 | DivisionsOrDegrees_1=1 | 0 | DivisionsOrDegrees_1=0
192 | Index | FixedOrFile_1 | 0 | 572 | 575 |  | C4 | 196 | Ä |  | 0 | 4 |  |  |  | FixedOrFile_1=0 | 0 | FixedOrFile_1=0 | 1 | FixedOrFile_1=1
193 | Index | Size_1 | 60.35 | 352 | 359 |  | BF | 191 | ¿ |  | 0 | 8 |  |  |  | Size_1=60.35 | 60 | Size_1=60 | 11 | Size_1=11
194 |  | ;Index 2 |  |  |  |  |  |  |  |  |  |  |  |  |  | ;Index 2 |  | ;Index 2 |  | ;Index 2
195 | Index | DivisionsOrDegrees_2 | 1 | 160 | 163 |  | 45 | 69 | E |  | 0 | 4 |  |  |  | DivisionsOrDegrees_2=1 | 1 | DivisionsOrDegrees_2=1 | 0 | DivisionsOrDegrees_2=0
196 | Index | FixedOrFile_2 | 0 | 708 | 711 |  | C4 | 196 | Ä |  | 0 | 4 |  |  |  | FixedOrFile_2=0 | 0 | FixedOrFile_2=0 | 1 | FixedOrFile_2=1
197 | Index | Size_2 | 22.5 | 360 | 367 |  | BF | 191 | ¿ |  | 0 | 8 |  |  |  | Size_2=22.5 | 180 | Size_2=180 | 180 | Size_2=180
198 |  | ;Index 3 |  |  |  |  |  |  |  |  |  |  |  |  |  | ;Index 3 |  | ;Index 3 |  | ;Index 3
199 | Index | DivisionsOrDegrees_3 | 1 | 152 | 155 |  | 45 | 69 | E |  | 0 | 4 |  |  |  | DivisionsOrDegrees_3=1 | 1 | DivisionsOrDegrees_3=1 | 0 | DivisionsOrDegrees_3=0
200 | Index | FixedOrFile_3 | 0 | 592 | 595 |  | C4 | 196 | Ä |  | 0 | 4 |  |  |  | FixedOrFile_3=0 | 0 | FixedOrFile_3=0 | 1 | FixedOrFile_3=1
201 | Index | Size_3 | 11.24 | 580 | 587 |  | BF | 191 | ¿ |  | 0 | 8 |  |  |  | Size_3=11.24 | 45 | Size_3=45 | 11 | Size_3=11
202 |  | ;Index 4 |  |  |  |  |  |  |  |  |  |  |  |  |  | ;Index 4 |  | ;Index 4 |  | ;Index 4
203 | Index | DivisionsOrDegrees_4 | 0 | 428 | 431 |  | 45 | 69 | E |  | 0 | 4 |  |  |  | DivisionsOrDegrees_4=0 | 0 | DivisionsOrDegrees_4=0 | 1 | DivisionsOrDegrees_4=1
204 | Index | FixedOrFile_4 | 0 | 588 | 591 |  | C4 | 196 | Ä |  | 0 | 4 |  |  |  | FixedOrFile_4=0 | 0 | FixedOrFile_4=0 | 1 | FixedOrFile_4=1
205 | Index | Size_4 | 180 | 672 | 679 |  | BF | 191 | ¿ |  | 0 | 8 |  |  |  | Size_4=180 | 4 | Size_4=4 | 11 | Size_4=11
206 |  | ;Index 5 |  |  |  |  |  |  |  |  |  |  |  |  |  | ;Index 5 |  | ;Index 5 |  | ;Index 5
207 | Index | DivisionsOrDegrees_5 | 0 | 440 | 443 |  | 45 | 69 | E |  | 0 | 4 |  |  |  | DivisionsOrDegrees_5=0 | 0 | DivisionsOrDegrees_5=0 | 1 | DivisionsOrDegrees_5=1
208 | Index | FixedOrFile_5 | 0 | 536 | 539 |  | C4 | 196 | Ä |  | 0 | 4 |  |  |  | FixedOrFile_5=0 | 0 | FixedOrFile_5=0 | 1 | FixedOrFile_5=1
209 | Index | Size_5 | 45 | 680 | 687 |  | BF | 191 | ¿ |  | 0 | 8 |  |  |  | Size_5=45 | 5 | Size_5=5 | 111 | Size_5=111
210 |  | ;Synchronize M3 and Spindle |  |  |  |  |  |  |  |  |  |  |  |  |  | ;Synchronize M3 and Spindle |  | ;Synchronize M3 and Spindle |  | ;Synchronize M3 and Spindle
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

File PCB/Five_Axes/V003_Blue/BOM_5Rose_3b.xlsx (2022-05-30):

Designator | MPN/Seeed SKU | Qty | Link
J22,J23,J47,J48,J49,J50,J51,J52,J53,J50 | F185-1208A0BSYA1 | 10 | https://statics3.seeedstudio.com/fusion/opl/datasheet/320030087.pdf
J41,J42 | A2541HWV-5P | 2 | https://www.cjt.com/upload/A2541.pdf
J5,J18 | A2541HWV-2P | 2 | https://www.cjt.com/upload/A2541.pdf
J4,J13 | A2541HWV-24P | 2 | https://www.cjt.com/upload/A2541.pdf
J19 | A2541HWV-2x5P | 1 | https://www.cjt.com/upload/A2541.pdf
J29 | A2541HWV-2x4P | 1 | https://www.cjt.com/upload/A2541.pdf
J34,J36 | A2541HWV-2x6P | 2 | https://www.cjt.com/upload/A2541.pdf
JP1,JP2 | P125-1103A1BS116A1 | 2 | https://statics3.seeedstudio.com/fusion/opl/datasheet/320020079.pdf
JP16 | P125-1102A0BS116A1 | 1 | https://statics3.seeedstudio.com/fusion/opl/datasheet/320020016.pdf
J7,J8,J24,J25,J37 | A2541WV-2x3P | 5 | https://www.cjt.com/upload/A2541.pdf
J6, J20, J21, J26, J31, J32 | 0022272041 | 6 | https://www.digikey.com/en/products/detail/molex/0022272041/1130579?s=N4IgTCBcDaIAxzEg7GOAWAjCAugXyA
J1,J2,J3,J10,J17,J35 | 1844236 | 6 | https://www.digikey.com/en/products/detail/phoenix-contact/1844236/349197
C1,C2,C3,C4,C5,C6 | KM101M050F115A | 6 | http://file.elecfans.com/web1/M00/69/50/o4YBAFvX9vSANgGQAAOqZzJWWPs538.pdf
U2 | R-78E5.0-1.0 | 1 | https://www.digikey.com/en/products/detail/recom-power/R-78E5-0-1-0/4930585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
R1 | FRC0603F5103TS | 1 | https://file.elecfans.com/web2/M00/2A/22/poYBAGHJGi2AZxKCABJssmAVZ38265.pdf?FRC_FOJAN.pdf
IC1,IC2 | SN74HCT245PW | 2 | https://www.digikey.com/en/products/detail/texas-instruments/SN74HCT245PW/1571518

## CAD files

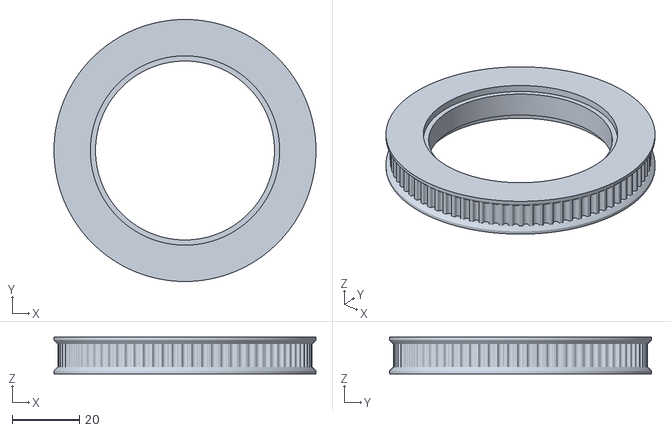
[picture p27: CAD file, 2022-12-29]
Hardware/GT2-3mm-80t_53.4-56.stl
78.1 x 78.1 x 11.0

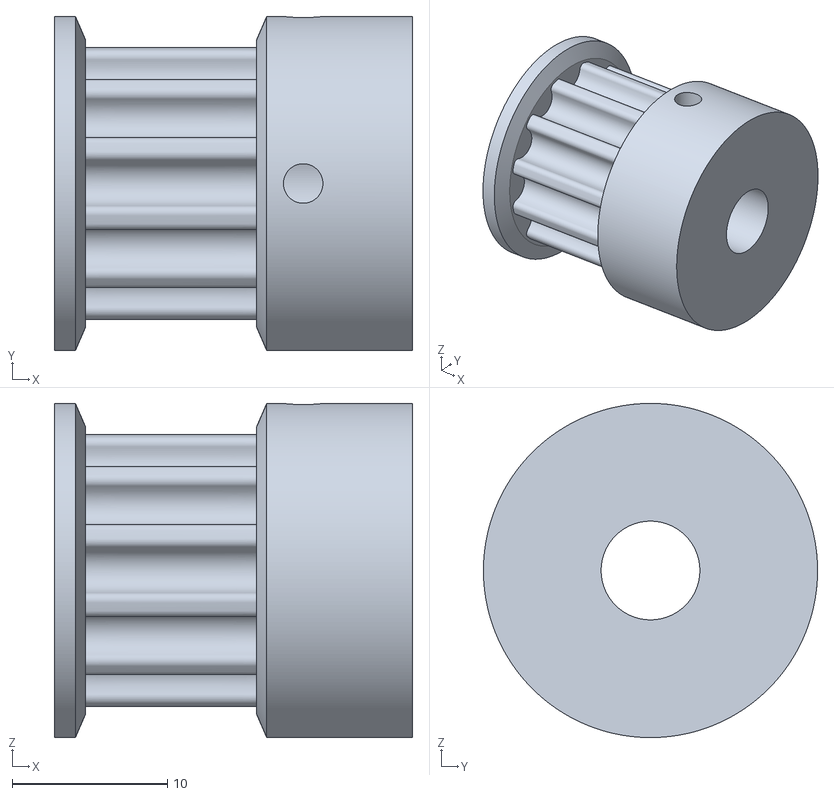
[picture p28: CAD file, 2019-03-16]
Hardware/GT2-5mm-12t/GT2-5mm_12T_6.35mmBore.stl
23.0 x 21.5 x 21.5

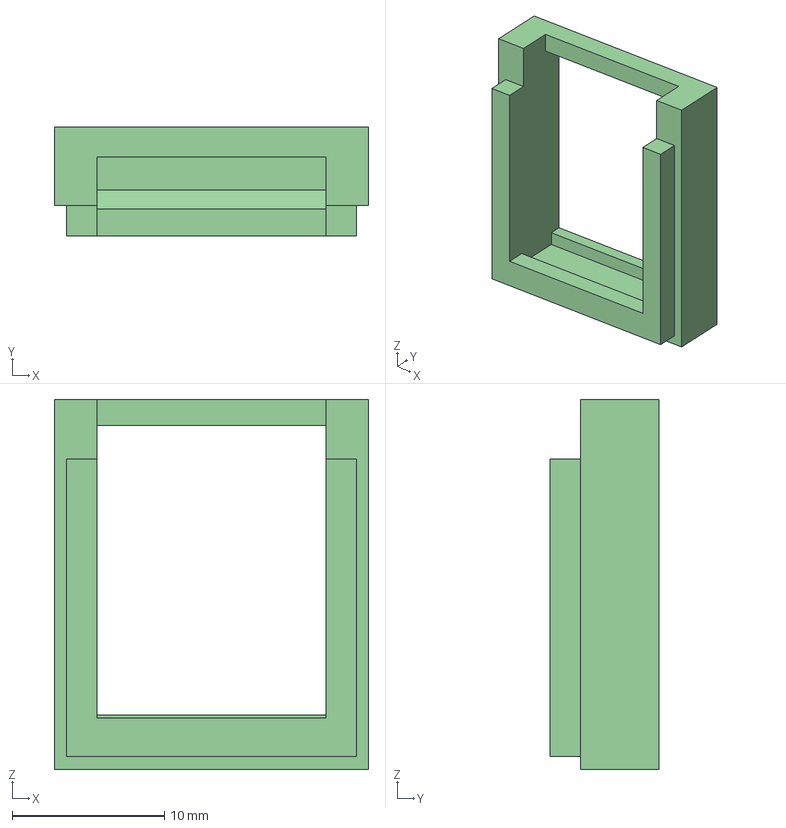
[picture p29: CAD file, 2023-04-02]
Hardware/Stepper-RJ45-Endcaps/RJ45_Panel_Adaptor v5.3mf
20.6 x 7.12 x 24.3 mm

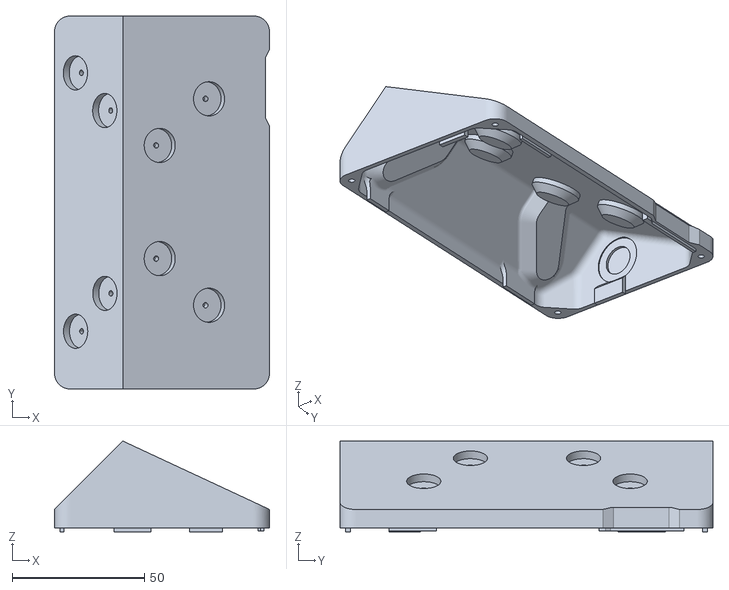
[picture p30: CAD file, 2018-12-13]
Nextion/Enclosure_43/Nextion_43_Base_v4.stl
81.3 x 141.0 x 34.4

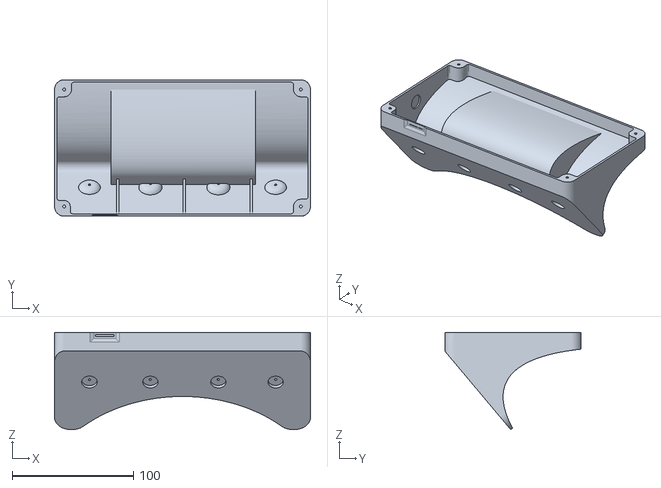
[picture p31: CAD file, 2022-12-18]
Nextion/Enclosure_7i/7i_Enclosure_03a/7i_Base_03a.stl
210.9 x 112.4 x 80.2

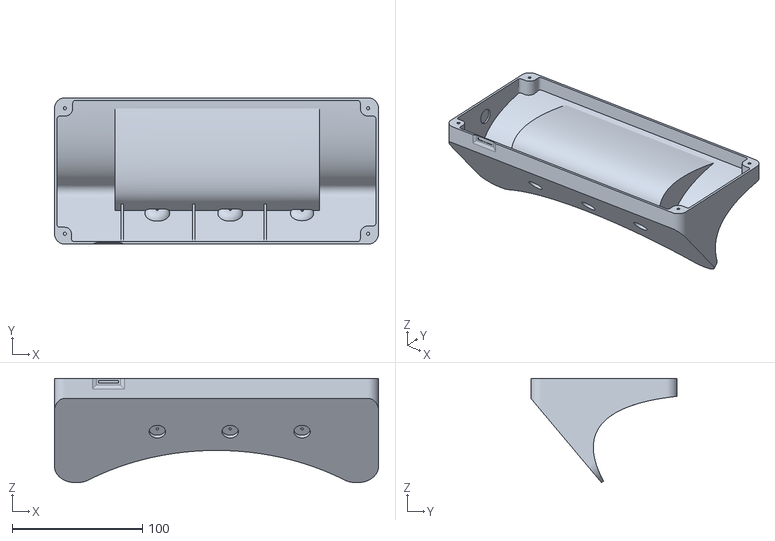
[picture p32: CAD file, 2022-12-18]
Nextion/Enclosure_7i/7i_Enclosure_03e/7i_Base_03e.stl
248.9 x 112.4 x 80.2

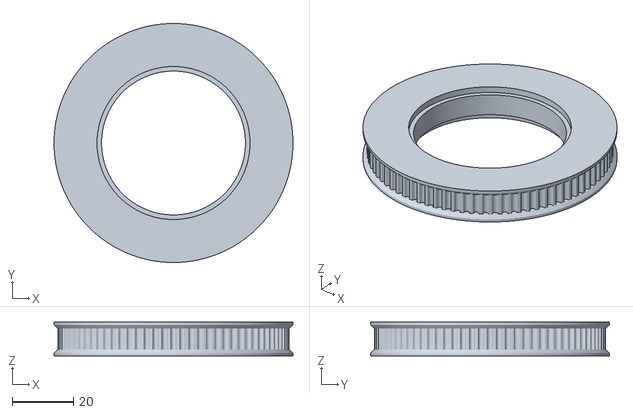
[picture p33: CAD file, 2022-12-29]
Hardware/GT2-3mm-80t_50-47.stl
78.1 x 78.1 x 11.0

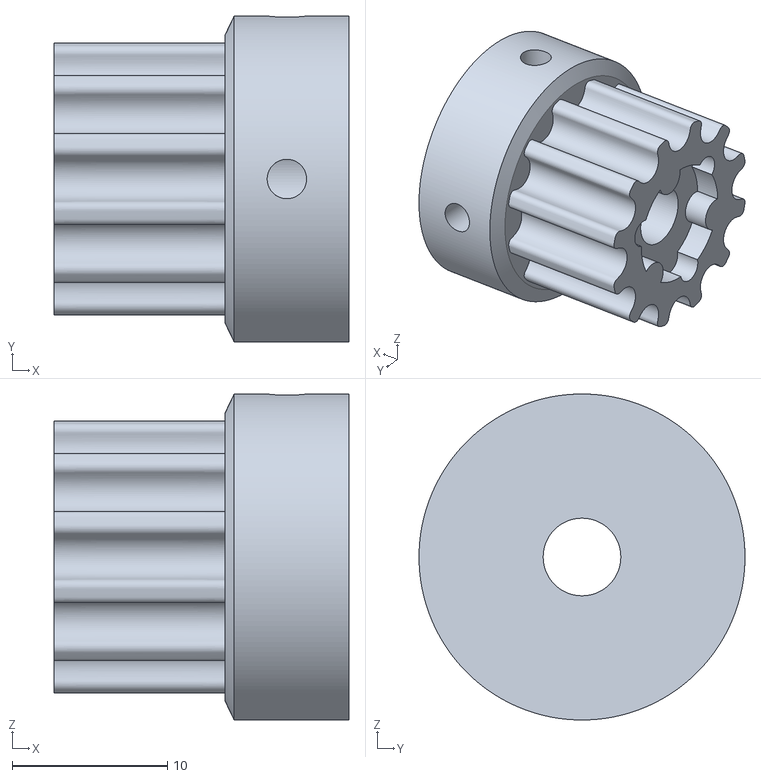
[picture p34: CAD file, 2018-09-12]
Hardware/GT2-5mm-12t/GT2-5mm_12t_3dPrint.stl
19.0 x 21.0 x 21.0

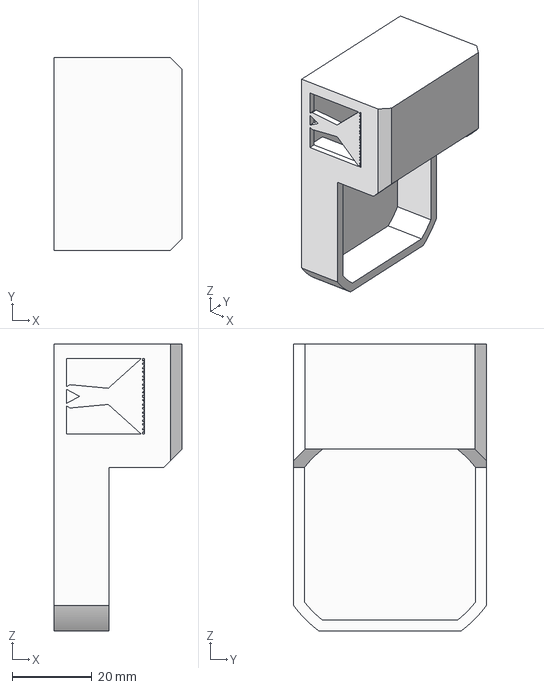
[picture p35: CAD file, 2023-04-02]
Hardware/Stepper-RJ45-Endcaps/RJ45_EndCap_NEMA17 v3.3mf
32.0 x 48.3 x 72.0 mm

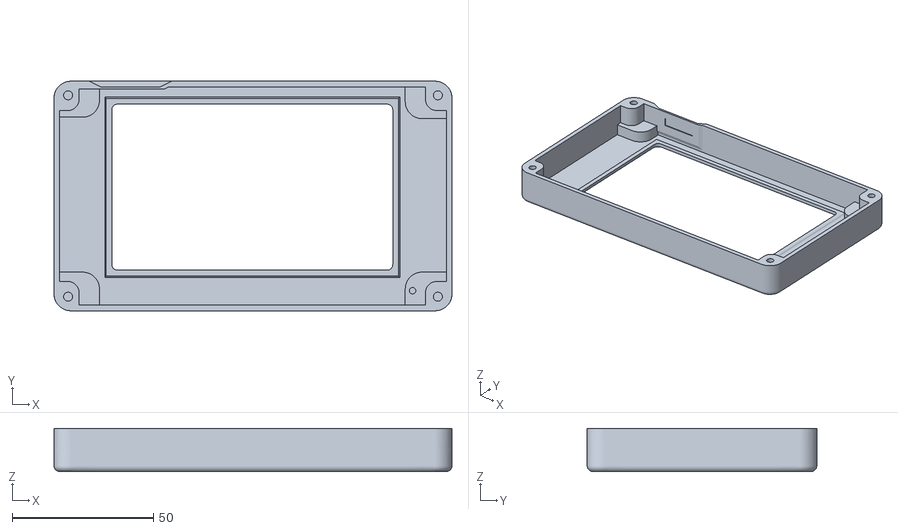
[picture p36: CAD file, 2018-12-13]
Nextion/Enclosure_43/Nextion_43_Bezel_v4.stl
141.1 x 81.4 x 15.2

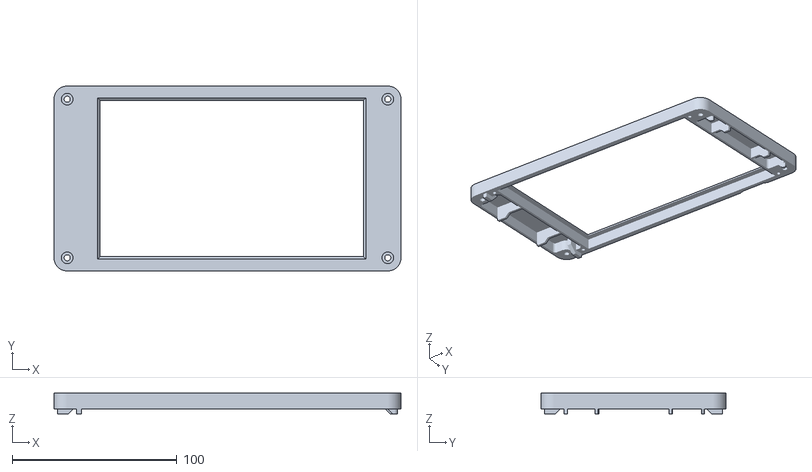
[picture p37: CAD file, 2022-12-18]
Nextion/Enclosure_7i/7i_Enclosure_03a/7i_Bezel_03a.stl
210.9 x 112.4 x 12.5

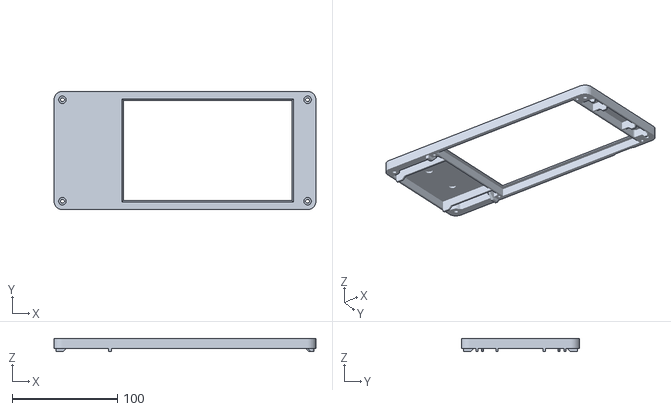
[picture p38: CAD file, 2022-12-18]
Nextion/Enclosure_7i/7i_Enclosure_03e/7i_Bezel_03e.stl
248.9 x 112.4 x 12.5

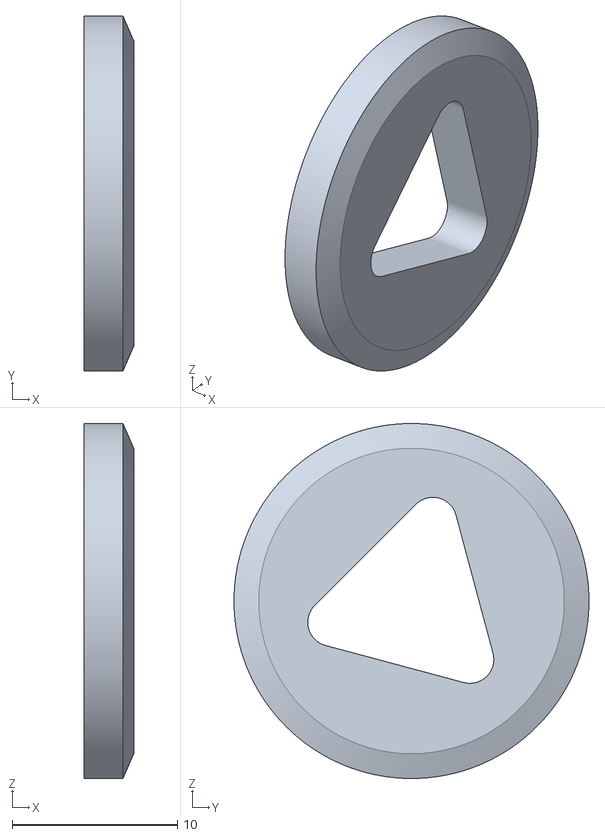
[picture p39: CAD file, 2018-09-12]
Hardware/GT2-5mm-12t/GT2_5_12t_Outer_Flange_3dPrint.stl
3.00 x 21.5 x 21.5

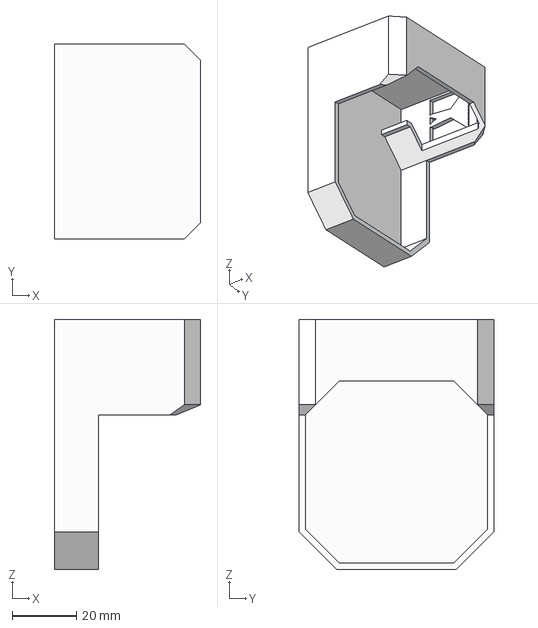
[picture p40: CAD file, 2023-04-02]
Hardware/Stepper-RJ45-Endcaps/RJ45_EndCap_NEMA23 v3.3mf
45.5 x 60.5 x 77.6 mm

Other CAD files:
Hardware/GT2-5mm-12t/GT2-5_12t_635mmBore.f3d
Hardware/Stepper-RJ45-Endcaps/RJ45_EndCap_NEMA17.f3z
Hardware/Stepper-RJ45-Endcaps/RJ45_EndCap_NEMA23.f3z
Nextion/Enclosure_43/Nextion43_BaseAndBezel.f3d

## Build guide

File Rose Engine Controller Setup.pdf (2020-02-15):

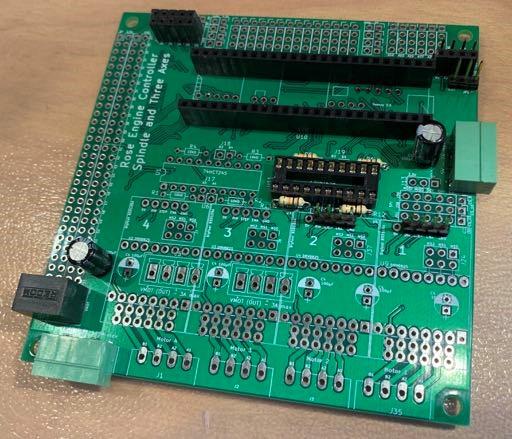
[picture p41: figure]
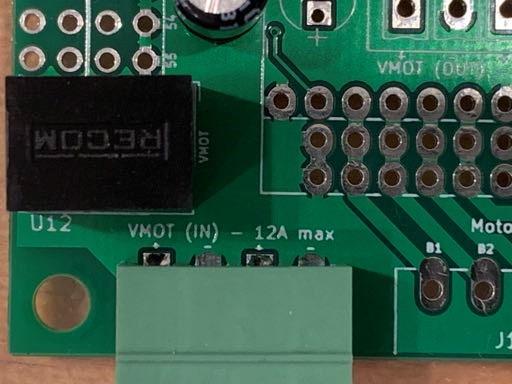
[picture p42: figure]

Rose Engine Controller Setup | – 1 – | v1 – 081519

### Rose Engine Controller Setup

Connecting, Installing & Upgrading the Rose Engine Controller Board
2 Axis, 4 Driver Controller
V011 / N11 - 08-15-19

The Rose Engine Controller board system is designed to drive the spindle and a second motor, to create a variety of ornamental patterns. The system is technically a two-axis, four motor control system. The controller board is combined with a Nextion touchscreen which enables selecting and using one or two motors, of up to four motors that can be controlled by the system. The user interface enables selecting from a variety of modes, running the motors individually or in combinations to produce complex patterns associated with ornamental turning.

The “brains” of the controller is a Teensy 3.5 made by PJRC (https:// www.pjrc.com). The Teensy version 3.5 features a 32 bit 120 MHz ARM CortexM4 processor with floating point unit.

The user interface for the system is based on an enhanced version a Nextion 4.3” touchscreen. The touchscreen is powered by, and communicates with the Teensy.

The controller board was designed to be very flexible in how it is adapted to each individual installation, so there are many options that will be discussed throughout this document. Choose the options best for your specific lathe and application.

### Connections

Power — Some form of power must be provided to the controller board, which in turn also supplies power to the Nextion touchscreen. There are xx options:

1) Supply 24V to the Vmot (IN) connector at the edge of the board. 24V is suggested, but your driver selection may determine a lower or higher voltage. The onboard DC-DC converter with accept 8V-42V and convert anything in that range to the 5V required for the Teensy and Nextion. Do not exceed 12 amps (12A) maximum. This is the preferred connection if onboard drivers are used, as the Vmot will be passed through the board to the drivers (and motors) and also power the Teensy and Nextion.

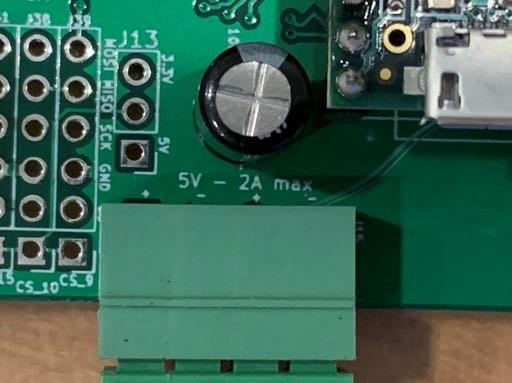
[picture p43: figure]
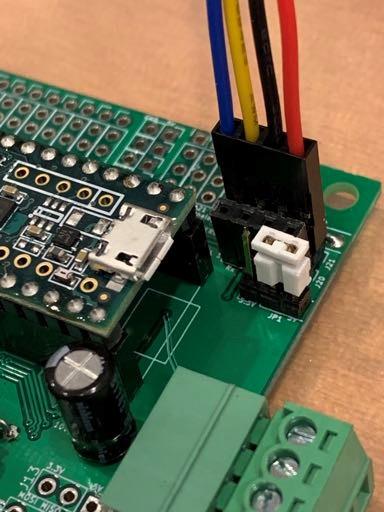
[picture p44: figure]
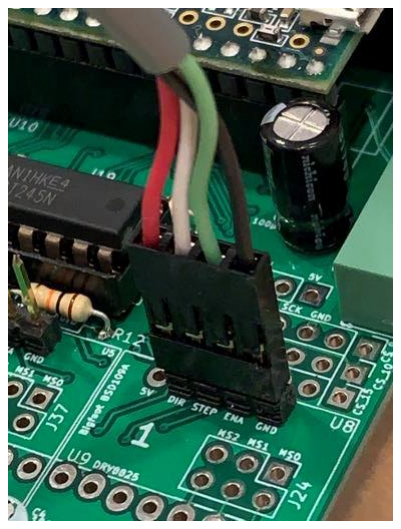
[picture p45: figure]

Rose Engine Controller Setup | – 2 – | v1 – 081519
2) Supply 5V directly to the edge connector. 2 amps maximum. This connection option is provided for those who will be using external (off board) drivers, and eliminates the need for a DC-DC converter to be installed on the controller.
3) Supply 24V to Vmot and then out of Vmot to an external DC-DC converter, then back to the 5V input.

Touchscreen — The Nextion touchscreen needs to get power from from the controller board, and communicate with the Teensy. This is done by connecting a four wire connector from the Serial3 port, near the USB end of the Teensy. Because the Nextion requires 5V to power the display, there is a 3-position jumper adjacent to the serial port, which allows selecting 3.3V or 5V. A jumper needs to connect the center pin with the pin closest to the outer edge of the board to provide 5V to the Nextion. This may also be a soldered (permanent) jumper wire.

The interconnect wire must have the “red” wire oriented towards the outside edge of the controller board. The other end is connected to a polarized socket on the underside of the Nextion touchscreen.

Stepper Drivers – One of the main goals of the controller board design was to
accommodate a variety of stepper driver usage scenarios. Small, low-current drivers
can be added on board, while larger current drivers can be mounted externally and
connected back to the controller board. Any combination of drivers can be connected to the controller. There are two options.
1) Onboard DRV8825 drivers – There are four locations for sockets to be added to the controller board that can accept Pololu DRV8825 drivers (https://www.pololu.com/product/2982). One to four drivers can be installed and used in any combination with external drivers. The DRV8825 drivers can be used with stepper motors up to 1.5A with no heatsink, and up to 2.2A with heatsinks and fan cooling. See the Pololu documentation for current setting and use of jumpers for microstepping settings.

If Vmot is brought into the controller board, then the motor edge connectors (Motor 1, Motor 2, etc.) can be used for direct connection and output to stepper motors from the board (maximum of 12A combined).

2) External “industrial style” drivers – There are four header locations on the controller
board to provide signals out to external “industrial style” stepper drivers. These are typically used for higher current motors, or for the convenience of selecting the motor current settings via DIP switches on the drivers. External drivers are connected using a “common ground” scheme, where the “–” terminals on the driver are connected to the GND (ground) pin on the controller, and the “+” terminals are connected to the individual signals (ENA = enable, DIR = direction and PUL = pulse or step).

Typically “black” colored wires will be used for ground (GND) connections. Note the
polarity of the header connector, with the black wire going to the GND pin on the
board.

Onboard Bigfoot drivers – The controller was originally designed to accommodate a mid-size driver that allowed using motors up to 3A, the Bigfoot BSD109A drivers (http://www.panucatt.com/product_p/bsd109a.htm). This was never successfully tested, and has been eliminated from future designs.

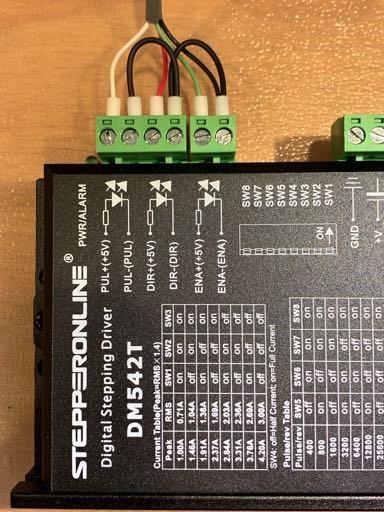
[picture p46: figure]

Rose Engine Controller Setup | – 3 – | v1 – 081519

Stepper Motors – If onboard drivers are used, connect the appropriate pairs of motor wires to the onboard connectors.

External Driver Connections – If using external drivers, connect the “–” terminals on the driver to the black (GND) wire and jumper to all three signals, ENA (enable), DIR (direction), and PUL (aka Step).

Teensy Pin and Breadboard Connections – The controller has numerous connection options for accessing the unused pins of the Teensy 3.5. These might be used for limit switches, other peripherals, and communications to other devices in the future. These is also a “breadboard” provision on the controller board to allow user additions and modifications for user-specific purposes. There are numerous locations to access 3.3V and 5V power, as well as GND connection near all the pins, allowing for easy button or other uses in conjunction with Arduino-style “pinMode(xx, INPUT_PULLUP)” mode.

### Installing Software

In order to use the system, software must be installed on both the Teensy 3.5 and the Nextion touchscreen. The repository for the project software, RoseEngine_SpindleAndAxis is located on Github at https://github.com/elfren/RoseEngine_SpindleAndAxis.

Teensy 3.5 – There is a .hex file for the Teensy 3.5 in the Teensy directory, in a sub-directory names Teensy35. The .hex file (currently named 4Rose_Vxxx.hex) can be loaded onto the Teensy 3.5 using the Teensy Loader utility https://www.pjrc.com/teensy/loader.html (which requires prior installation of the Arduino IDE https:// www.arduino.cc/en/Main/Software and Teensyduino extension https://www.pjrc.com/teensy/td_download.html (https://www.pjrc.com/teensy/td_download.html) … not for the faint of heart …

Nextion – Similar to the Teensy, the Nextion touchscreen needs to have software installed on it as well. The software for the Nextion is in the Nextion directory, in the Four_Axes subdirectory, named RoseEngin_Nxx.tft. This file needs to be copied to a microSD card and inserted into the Nextion’s card slot. Either connected to the controller board, or using the Nextion supplied USB adapter board and a USB Micro B cable, supply power to the touchscreen. It will detect and install the .tft file. After installation, remove the microSD card to run the system.

### First Use Initialization

Prior to first use, numerous values need to be initialized via the Teensy and values stored in the Nextion. To make this easier a file named 4Axes.ini is at the top level of the repository. This file needs to be copied to a microSD card and inserted into the card slot on the Teensy 3.5. When the system is powered on, the “splash screen” on the Nextion will have a button in the lower right corner that will allow the .ini file to be read and values stored. After the file has been copied successfully, shut down, remove the card and re-boot the system.

Rose Engine Controller Setup | – 4 – | v1 – 081519

### Mounting

When mounting the Nextion touchscreen, note that the microSD card slot is oriented towards the bottom edge in our configurations. This is intended to minimize the possibility of any dust contamination when being used on the lathe.

### Cautions

- Never disconnect a stepper motor from a stepper driver when the system is powered.
- All components and boards are sensitive to static electricity. Use precautions when handling.

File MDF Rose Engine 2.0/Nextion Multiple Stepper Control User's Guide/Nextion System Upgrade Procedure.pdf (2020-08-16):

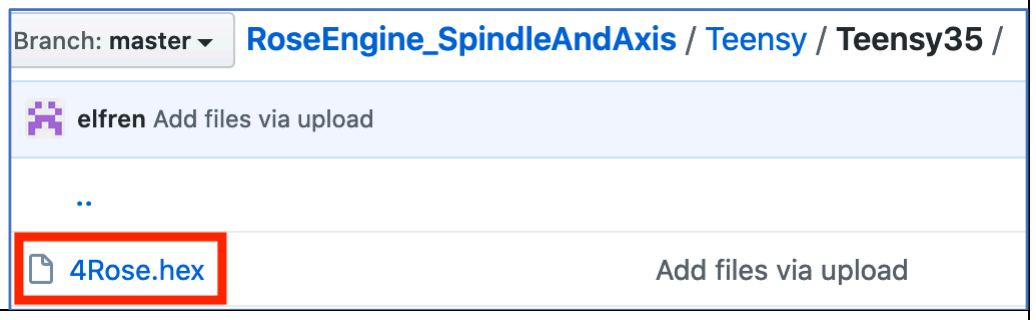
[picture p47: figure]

### Step 1 – Get a copy of the Teensy program file

Download 4Rose.hex to your computer.

### Step 2 – Get a copy of the Nextion configuration file

Download RoseEngine_14.tft, and put it in the root folder of a microSD card.

Notes:
1. You can only have one file on this card which is a .TFT file. The upgrade will not work if there is a 2d one.
2. You need to check for hidden
files on the microSD card. I
found that hard to do on

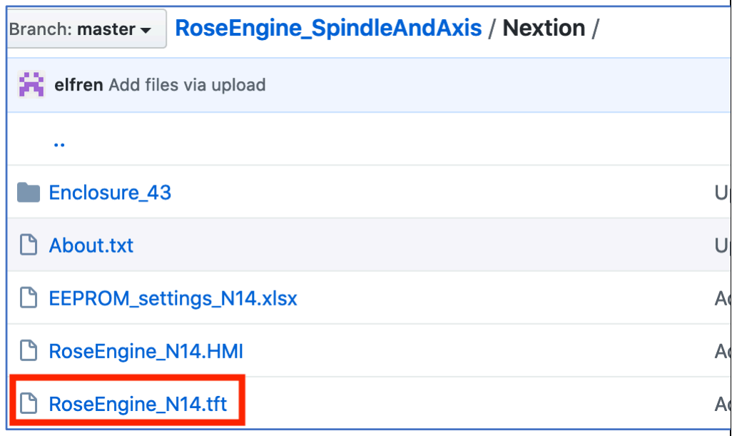
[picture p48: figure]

macOS (which created a hidden TFT file) and had to do this on a Raspberry Pi.

### Step 3 – Get a copy of the 4Axes.ini settings file

Download 4Axes.ini, and put it in the root of a second microSD card

### Step 4 - Upgrade the Teensy

Step 4a
Connect the computer to the Teensy.

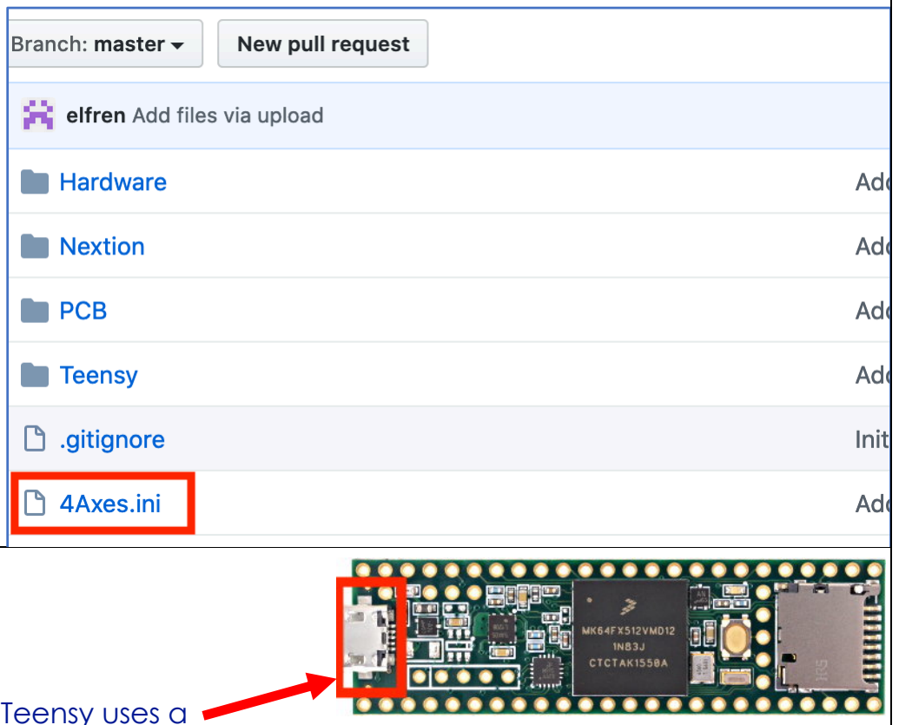
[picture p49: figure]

- The cable end connected to the Teensy uses a MicroUSB connector.
- The Teensy’s jack is noted in the picture to the right.

Notes:
1. Be sure you have a good MicroUSB cable. Some are only used for charging a device (and they are usually longer). These will often not work.

Step 4b

On the Computer, start the Teensy Loader. The icon looks like the one to the right.

Note:
1. If you don’t have the Teensy Loader, you can get it from https://www.pjrc.com/teensy/loader.html.
Step 4c

Be sure the system shows that the Teensy is connected. This is evident when the Auto button is illuminated green. As noted in step 4a above, if your USB cable is bad, this won’t light.

The default for the CPU selected won’t handle the whole 4Rose.hex file, so if you try to open it, you will get the message as shown here.

Step 4d

Press the button on the Teensy to load the get the Teensy loader to recognize which CPU you are using.

Step 4e

Back on the Computer, using the Teensy Loader, open 4Rose.hex.

Once this is loaded, the bottom message will change to reflect the file size. (this picture was not updated).

Step 4f

Press the button on the Teensy to load the program file.

Disconnect the computer from the Teensy, and then reboot the Teensy.

### Step 5 – Upgrade the Nextion

Secure the microSD card which has the Nextion configuration file (from step 2).

Put this microSD card into the Nextion’s microSD card slot.

Reboot the Teensy again.

If this works as expected, it will read that it is “successed” (guess that is a bad translation from Chinese).

After that message appear, remove the
microSD card from the Nextion.

### Step 6 - Load the .ini file

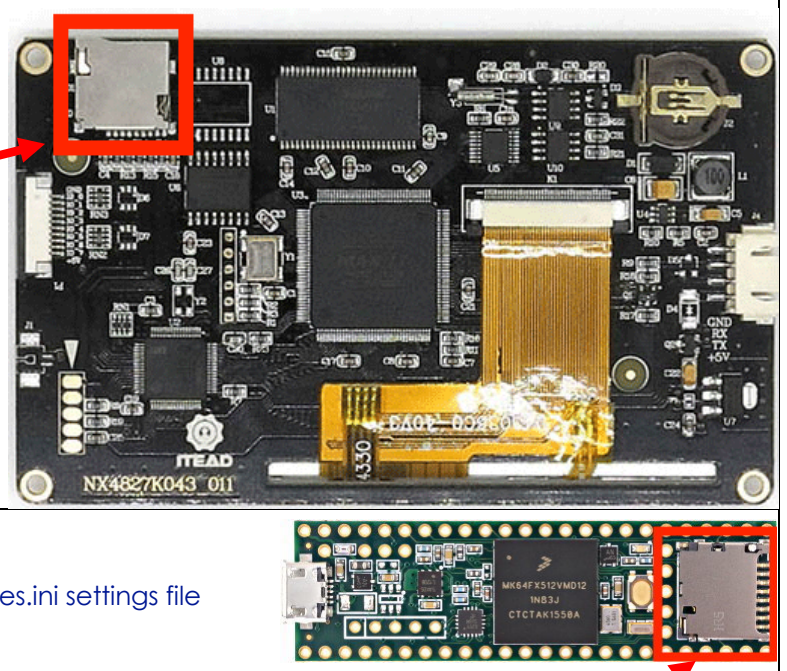
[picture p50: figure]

Secure the microSD card which has the 4Axes.ini settings file (from step 3).

Put this microSD card into the Teensy’s microSD card slot.

Start the system and click the Load ini button.

The Load ini button will turn green, and then it will
take off. Once completed, a message will appear saying to reboot the system.

Reboot the system one last time.

### Step 7 – Verify the Settings

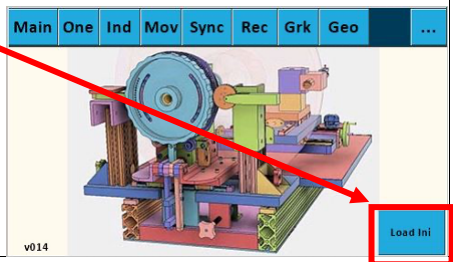
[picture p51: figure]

It's a good practice to verify all of the settings once you've completed the steps.

1. Touch the Config button on each page and verify the Teensy column is populated with the same numbers as the Nextion column. Repeat for each axis on each page.
2. Next verify the Preferences are correct for the Spindle, Axes, Limits, and Returns.
3. Select the Main page, then the '...' (Preferences) page. Select the More page. Touch EEPROM. Repeat for each page and axis on the page. This will show all of the settings for the selected page.
A copy of the settings file (4Axes.ini) is on the following sheets.

### Config file settings

;==================================== [Setup]
;==================================== BoardType=4
Microsteps_Spindle=32
StepsPer360_Spindle=200
GearRatio_Spindle=9
Polarity_Spindle=1

;Z Axis
Microsteps_Z=32
StepsPer360_Z=200
DistancePer360_Z=.02
Polarity_Z=1

;X Axis
Microsteps_X=32
StepsPer360_X=200
DistancePer360_X=.02
Polarity_X=1

;B Axis
Microsteps_B=32
StepsPer360_B=200
GearRatio_B=150
Polarity_B=1
DistancePer360_B=1.02
RadialOrLineal=0
BRadius=5

;==================================== [Limits]
;==================================== ;Limit Switches
Min_Z=34
Max_Z=35
Min_X=36
Max_X=37
Min_B=38
Max_B=39

;==================================== [Returns]
;==================================== ;Return
MaxSpeed_Spindle=15011
Accel_Spindle=15012

MaxSpeed_Axis_Z=15013
Accel_Axis_Z=15014

MaxSpeed_Axis_X=15015
Accel_Axis_X=15016

MaxSpeed_Axis_B=15017
Accel_Axis_B=15018

;==================================== [Main]
;==================================== ;Axis Ids:
;-----------------
;Z=0
;X=1
;B=2
;Spindle=3

;-----------------
AxisId=0
;Spindle
MaxSpeed_Spindle=15000
Accel_Spindle=15001
SpeedPercentage_Spindle=30

;Z Axis
MaxSpeed_Z=4001
Accel_Z=5002
SpeedPercentage_Z=53

;X Axis
MaxSpeed_X=4000
Accel_X=5005
SpeedPercentage_X=10

;B Axis
MaxSpeed_B=5007
Accel_B=5008
SpeedPercentage_B=59

;==================================== [One]
;==================================== AxisId=3
;Spindle
MaxSpeed_Spindle=25060
Accel_Spindle=20061
SpeedPercentage_Spindle=61 ;Z Axis
MaxSpeed_Z=5062
Accel_Z=5063
SpeedPercentage_Z=64
;X Axis
MaxSpeed_X=5065
Accel_X=5066
SpeedPercentage_X=67
;B Axis
MaxSpeed_B=5068
Accel_B=5069
SpeedPercentage_B=70

;==================================== [Ind]
;==================================== IndexId=1
MaxSpeed_Spindle=5070
Accel_Spindle=5071
SpeedPercentage_Spindle=72 ;-----------------
;Division:0 Degrees:2
;Fixed:0 File:1
;-----------------
;Index 1
DivisionsOrDegrees_1=2
FixedOrFile_1=0
Size_1=1.875
;Index 2
DivisionsOrDegrees_2=2
FixedOrFile_2=0
Size_2=24.375
;Index 3
DivisionsOrDegrees_3=2
FixedOrFile_3=0
Size_3=90

;==================================== [Mov]
;==================================== AxisId=0
;Z Axis
MaxSpeed_Z=5080
Accel_Z=5081
SpeedPercentage_Z=82
Distance_Z=3

;X Axis
MaxSpeed_X=5083
Accel_X=5084
SpeedPercentage_X=85
Distance_X=5.75

;B Axis
MaxSpeed_B=5086
Accel_B=5087
SpeedPercentage_B=88
Distance_B=5.78

;==================================== [BE]
;==================================== AxisId=0
;Spindle
MaxSpeed_Spindle=5090
Accel_Spindle=5091
SpeedPercentage_Spindle=92

;Z Axis
MaxSpeed_Z=5093
Accel_Z=5094
SpeedPercentage_Z=95

;X Axis
MaxSpeed_X=5096
Accel_X=5097
SpeedPercentage_X=98

;B Axis
MaxSpeed_B=5099
Accel_B=5100
SpeedPercentage_B=50

;==================================== [Sync]
;==================================== AxisId=0
HelixType=0
Revolutions=.3
Distance=10
;Spindle
MaxSpeed_Spindle=5040
Accel_Spindle=5041
SpeedPercentage_Spindle=42

;Z Axis
MaxSpeed_Z=5043
Accel_Z=5044
SpeedPercentage_Z=45

;X Axis
MaxSpeed_X=5046
Accel_X=5047
SpeedPercentage_X=48

;B Axis
MaxSpeed_B=5048
Accel_B=5049
SpeedPercentage_B=49

;==================================== [Rec]
;==================================== AxisId=0
RadialOrAxial=0
;Spindle
MaxSpeed_Spindle=5030
Accel_Spindle=5031
SpeedPercentage_Spindle=32

;Z Axis
MaxSpeed_Z=5033
Accel_Z=5034
SpeedPercentage_Z=35

;X Axis
MaxSpeed_X=5036
Accel_X=5037
SpeedPercentage_X=38

;B Axis
MaxSpeed_B=5039
Accel_B=5040
SpeedPercentage_B=39

;Radial
Radial_Waves=5
Radial_Spindle_Amplitude=20 Radial_Axis_Distance=5

;Axial
Axial_Waves=4
Axial_Spindle_Degrees=25
Axial_Axis_Amplitude=7

;==================================== [Grk]
;==================================== AxisId=0
FileOrPattern=0
;Spindle
MaxSpeed_Spindle=5020
Accel_Spindle=5021
SpeedPercentage_Spindle=22

;Z Axis
MaxSpeed_Z=5023
Accel_Z=5024
SpeedPercentage_Z=25

;X Axis
MaxSpeed_X=5026
Accel_X=5027
SpeedPercentage_X=28

;B Axis
MaxSpeed_B=5028
Accel_B=5029
SpeedPercentage_B=29

;Pattern page
RadialOrAxial_Pattern=0
;4a: 2 4b: 3 3a: 6 3b: 7 2a: 4 2b: 5 PatternType=4
Pattern_PatternsPer360=8
Pattern_PatternCount=1
Pattern_SegmentLength=1

;File page
RadialOrAxial_File=0
File_PatternsPer360=7
File_PatternCount=1
File_SegmentLength=1

;Segments: 2 Actual: 3
File_SegmentsOrActual=2

;==================================== [Geo]
;==================================== AxisId=0
RadialOrAxial=0
Rose_n=7
Rose_d=5

;Spindle
MaxSpeed_Spindle=5010
Accel_Spindle=5011
SpeedPercentage_Spindle=12

;Z Axis
MaxSpeed_Z=5013
Accel_Z=5014
SpeedPercentage_Z=15
RadialAmplitude_Z=2
AxialAmplitude_Z=2.5

;X Axis
MaxSpeed_X=5016
Accel_X=5017
SpeedPercentage_X=18
RadialAmplitude_X=2
AxialAmplitude_X=2.5

;B Axis
MaxSpeed_B=5018
Accel_B=5019
SpeedPercentage_B=19
RadialAmplitude_B=3
AxialAmplitude_B=3.5

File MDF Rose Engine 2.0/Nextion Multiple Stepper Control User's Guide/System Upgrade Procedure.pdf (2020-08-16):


### Step 1 – Get a copy of the Teensy program file

Download 4Rose.hex to your computer.

### Step 2 – Get a copy of the Nextion configuration file

Download RoseEngine_14.tft, and put it in the root folder of a microSD card.

Notes:
1. You can only have one file on this card which is a .TFT file. The upgrade will not work if there is a 2d one.
2. You need to check for hidden
files on the microSD card. I
found that hard to do on


macOS (which created a hidden TFT file) and had to do this on a Raspberry Pi.

### Step 3 – Get a copy of the 4Axes.ini settings file

Download 4Axes.ini, and put it in the root of a second microSD card

### Step 4 - Upgrade the Teensy

Step 4a
Connect the computer to the Teensy.


- The cable end connected to the Teensy uses a MicroUSB connector.
- The Teensy’s jack is noted in the picture to the right.

Notes:
1. Be sure you have a good MicroUSB cable. Some are only used for charging a device (and they are usually longer). These will often not work.

Step 4b

On the Computer, start the Teensy Loader. The icon looks like the one to the right.

Note:
1. If you don’t have the Teensy Loader, you can get it from https://www.pjrc.com/teensy/loader.html.
Step 4c

Be sure the system shows that the Teensy is connected. This is evident when the Auto button is illuminated green. As noted in step 4a above, if your USB cable is bad, this won’t light.

The default for the CPU selected won’t handle the whole 4Rose.hex file, so if you try to open it, you will get the message as shown here.

Step 4d

Press the button on the Teensy to load the get the Teensy loader to recognize which CPU you are using.

Step 4e

Back on the Computer, using the Teensy Loader, open 4Rose.hex.

Once this is loaded, the bottom message will change to reflect the file size. (this picture was not updated).

Step 4f

Press the button on the Teensy to load the program file.

Disconnect the computer from the Teensy, and then reboot the Teensy.

### Step 5 – Upgrade the Nextion

Secure the microSD card which has the Nextion configuration file (from step 2).

Put this microSD card into the Nextion’s microSD card slot.

Reboot the Teensy again.

If this works as expected, it will read

Check Data … 100%
Updated Successed!

(guess that is a bad translation from
Chinese).

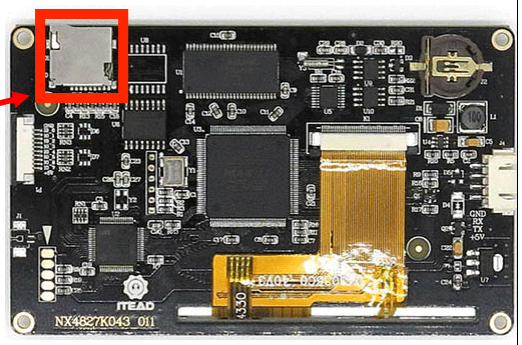
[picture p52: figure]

After that message appear, remove the microSD card from the Nextion, and reboot the Teensy again.

### Step 6 - Load the .ini file

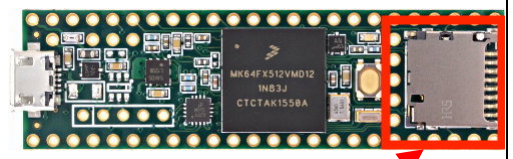
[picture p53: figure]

Secure the microSD card which has the 4Axes.ini settings file
(from step 3).

Put this microSD card into the Teensy’s microSD card slot.

Start the system and click the Load ini button.

The Load ini button will turn green, and then it will
take off.

Once completed, a message will appear saying

Done – Restart may be needed.

Reboot the system one last time.

### Step 7 – Verify the Settings

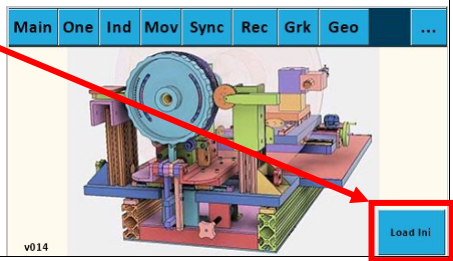
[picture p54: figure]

It's a good practice to verify all of the settings once you've completed the steps.

1. Touch the Config button on each page and verify the Teensy column is populated with the same numbers as the Nextion column. Repeat for each axis on each page.
2. Next verify the Preferences are correct for the Spindle, Axes, Limits, and Returns.
3. Select the Main page, then the '...' (Preferences) page. Select the More page. Touch EEPROM. Repeat for each page and axis on the page. This will show all of the settings for the selected page.
A copy of the settings file (4Axes.ini) is on the following sheets.

### Config file settings

;==================================== [Setup]
;==================================== BoardType=4
Microsteps_Spindle=32
StepsPer360_Spindle=200
GearRatio_Spindle=9
Polarity_Spindle=1

;Z Axis
Microsteps_Z=32
StepsPer360_Z=200
DistancePer360_Z=.02
Polarity_Z=1

;X Axis
Microsteps_X=32
StepsPer360_X=200
DistancePer360_X=.02
Polarity_X=1

;B Axis
Microsteps_B=32
StepsPer360_B=200
GearRatio_B=150
Polarity_B=1
DistancePer360_B=1.02
RadialOrLineal=0
BRadius=5

;==================================== [Limits]
;==================================== ;Limit Switches
Min_Z=34
Max_Z=35
Min_X=36
Max_X=37
Min_B=38
Max_B=39

;==================================== [Returns]
;==================================== ;Return
MaxSpeed_Spindle=15011
Accel_Spindle=15012

MaxSpeed_Axis_Z=15013
Accel_Axis_Z=15014

MaxSpeed_Axis_X=15015
Accel_Axis_X=15016

MaxSpeed_Axis_B=15017
Accel_Axis_B=15018

;==================================== [Main]
;==================================== ;Axis Ids:
;-----------------
;Z=0
;X=1
;B=2
;Spindle=3

;-----------------
AxisId=0
;Spindle
MaxSpeed_Spindle=15000
Accel_Spindle=15001
SpeedPercentage_Spindle=30

;Z Axis
MaxSpeed_Z=4001
Accel_Z=5002
SpeedPercentage_Z=53

;X Axis
MaxSpeed_X=4000
Accel_X=5005
SpeedPercentage_X=10

;B Axis
MaxSpeed_B=5007
Accel_B=5008
SpeedPercentage_B=59

;==================================== [One]
;==================================== AxisId=3
;Spindle
MaxSpeed_Spindle=25060
Accel_Spindle=20061
SpeedPercentage_Spindle=61 ;Z Axis
MaxSpeed_Z=5062
Accel_Z=5063
SpeedPercentage_Z=64
;X Axis
MaxSpeed_X=5065
Accel_X=5066
SpeedPercentage_X=67
;B Axis
MaxSpeed_B=5068
Accel_B=5069
SpeedPercentage_B=70

;==================================== [Ind]
;==================================== IndexId=1
MaxSpeed_Spindle=5070
Accel_Spindle=5071
SpeedPercentage_Spindle=72 ;-----------------
;Division:0 Degrees:2
;Fixed:0 File:1
;-----------------
;Index 1
DivisionsOrDegrees_1=2
FixedOrFile_1=0
Size_1=1.875
;Index 2
DivisionsOrDegrees_2=2
FixedOrFile_2=0
Size_2=24.375
;Index 3
DivisionsOrDegrees_3=2
FixedOrFile_3=0
Size_3=90

;==================================== [Mov]
;==================================== AxisId=0
;Z Axis
MaxSpeed_Z=5080
Accel_Z=5081
SpeedPercentage_Z=82
Distance_Z=3

;X Axis
MaxSpeed_X=5083
Accel_X=5084
SpeedPercentage_X=85
Distance_X=5.75

;B Axis
MaxSpeed_B=5086
Accel_B=5087
SpeedPercentage_B=88
Distance_B=5.78

;==================================== [BE]
;==================================== AxisId=0
;Spindle
MaxSpeed_Spindle=5090
Accel_Spindle=5091
SpeedPercentage_Spindle=92

;Z Axis
MaxSpeed_Z=5093
Accel_Z=5094
SpeedPercentage_Z=95

;X Axis
MaxSpeed_X=5096
Accel_X=5097
SpeedPercentage_X=98

;B Axis
MaxSpeed_B=5099
Accel_B=5100
SpeedPercentage_B=50

;==================================== [Sync]
;==================================== AxisId=0
HelixType=0
Revolutions=.3
Distance=10
;Spindle
MaxSpeed_Spindle=5040
Accel_Spindle=5041
SpeedPercentage_Spindle=42

;Z Axis
MaxSpeed_Z=5043
Accel_Z=5044
SpeedPercentage_Z=45

;X Axis
MaxSpeed_X=5046
Accel_X=5047
SpeedPercentage_X=48

;B Axis
MaxSpeed_B=5048
Accel_B=5049
SpeedPercentage_B=49

;==================================== [Rec]
;==================================== AxisId=0
RadialOrAxial=0
;Spindle
MaxSpeed_Spindle=5030
Accel_Spindle=5031
SpeedPercentage_Spindle=32

;Z Axis
MaxSpeed_Z=5033
Accel_Z=5034
SpeedPercentage_Z=35

;X Axis
MaxSpeed_X=5036
Accel_X=5037
SpeedPercentage_X=38

;B Axis
MaxSpeed_B=5039
Accel_B=5040
SpeedPercentage_B=39

;Radial
Radial_Waves=5
Radial_Spindle_Amplitude=20 Radial_Axis_Distance=5

;Axial
Axial_Waves=4
Axial_Spindle_Degrees=25
Axial_Axis_Amplitude=7

;==================================== [Grk]
;==================================== AxisId=0
FileOrPattern=0
;Spindle
MaxSpeed_Spindle=5020
Accel_Spindle=5021
SpeedPercentage_Spindle=22

;Z Axis
MaxSpeed_Z=5023
Accel_Z=5024
SpeedPercentage_Z=25

;X Axis
MaxSpeed_X=5026
Accel_X=5027
SpeedPercentage_X=28

;B Axis
MaxSpeed_B=5028
Accel_B=5029
SpeedPercentage_B=29

;Pattern page
RadialOrAxial_Pattern=0
;4a: 2 4b: 3 3a: 6 3b: 7 2a: 4 2b: 5 PatternType=4
Pattern_PatternsPer360=8
Pattern_PatternCount=1
Pattern_SegmentLength=1

;File page
RadialOrAxial_File=0
File_PatternsPer360=7
File_PatternCount=1
File_SegmentLength=1

;Segments: 2 Actual: 3
File_SegmentsOrActual=2

;==================================== [Geo]
;==================================== AxisId=0
RadialOrAxial=0
Rose_n=7
Rose_d=5

;Spindle
MaxSpeed_Spindle=5010
Accel_Spindle=5011
SpeedPercentage_Spindle=12

;Z Axis
MaxSpeed_Z=5013
Accel_Z=5014
SpeedPercentage_Z=15
RadialAmplitude_Z=2
AxialAmplitude_Z=2.5

;X Axis
MaxSpeed_X=5016
Accel_X=5017
SpeedPercentage_X=18
RadialAmplitude_X=2
AxialAmplitude_X=2.5

;B Axis
MaxSpeed_B=5018
Accel_B=5019
SpeedPercentage_B=19
RadialAmplitude_B=3
AxialAmplitude_B=3.5

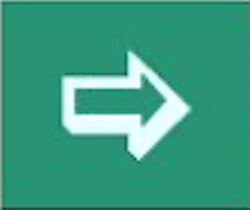
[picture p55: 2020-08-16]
MDF Rose Engine 2.0/Nextion Multiple Stepper Control User's Guide/Images/ButtonGreekKey-Out.png

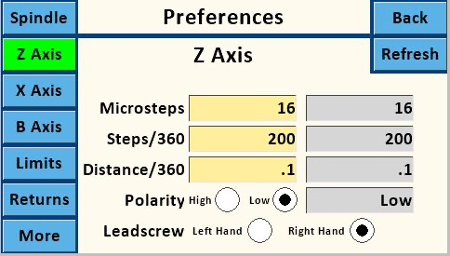
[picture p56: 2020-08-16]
MDF Rose Engine 2.0/Nextion Multiple Stepper Control User's Guide/Images/Nextion-Config-ZAxis.png

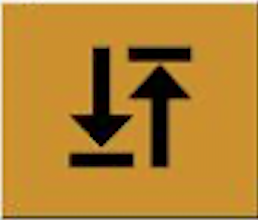
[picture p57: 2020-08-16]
MDF Rose Engine 2.0/Nextion Multiple Stepper Control User's Guide/Images/ButtonSync-Return.png

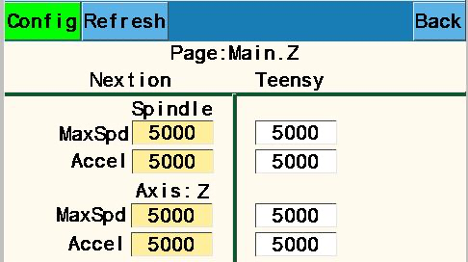
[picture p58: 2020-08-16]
MDF Rose Engine 2.0/Nextion Multiple Stepper Control User's Guide/Images/Nextion-Config-SpeedDir-Spindle.png

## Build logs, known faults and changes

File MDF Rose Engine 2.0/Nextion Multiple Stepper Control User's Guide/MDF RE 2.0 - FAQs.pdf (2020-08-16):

# MDF Rose Engine Lathe 2.0

# with Stepper Motor Drive

# Frequently Asked Questions

## Version 1.0 04 July 2020

## MDF Rose Engine 2.0 – FAQs

This document is intended to answer frequently asked questions about the rose engine lathe kit sold on www.ColvinTools.com.

If you have any questions, please contact us at ColvinTools@Gmail.com.

Good luck.

Rich Colvin & Jack Zimmel

### Table of Contents

## Frequently Asked Questions

The questions below are commonly asked, and responses are given to help the reader.

### General

Does this design accommodate both rocking and pumping?
This kit provides for rocking, and there have been a number of people who have adding pumping capabilities. That capability is not provided by this kit at this time. As this evolves over time, we will evaluate and consider adding it to the kit.
None-the-less, if you are new to ornamental turning, there are so many capabilities provided by this machine that it will probably be a long time before you find the lack of pumping to be a limitation to your artistic endeavors (at least I haven’t yet).

Does this design accommodate a barrel approach with more than two rosettes?
The use of more than two rosettes at one time is something not accommodated by the design of this lathe. Instead, the ability to easily switch rosettes is a design feature for this machine. And what are unique features for this machine are:
1. The ability to easily change the phasing of the rosettes without having to perform any calculations.
2. The ability to change the alignment of one rosette against another.
So, if you are new to ornamental turning, this machine will enable you to pursue your artistic endeavors easily and without having to spend great amounts of time learning how.

Where can I learn more about ornamental turning?
There are a number of great good options:
- Join the Ornamental Turners International (http://ornamentalturners.com). There is a forum on the web site which allows for questions to be posed and are typically answered relatively soon.
- Attend the Ornamental Turners International Symposium. There, you will meet many other users of the MDF rose engine lathe.
- Check out the “Ornamental Turning Book of Knowledge” (https://www.otbok.info). There is also a list of additional resources on that site.

### Spindle

May I get a spindle with spindle threads of 1-1/4”-8 (or M33)?
The kit as designed is for a spindle with threads of 1”-8. That is a standard for almost all rose engine lathes. Offering multiple options would also increase the cost of the kit too much, and that was a design criterion for the offering. A machine shop should be able to make a spindle for you with this threading if that is desired, but all the other variables will have to be examined.

May I get a spindle with a Morse taper?
This is being catered for in the design.

### Spindle Drive

Do you sell a kit with the hand crank as an option?
Haven spoken with a large number of MDF rose engine lathe users, all have motorized the spindle drive. Many have used geared motors with the speed controlled by changing the frequency of the power feed. Whilst that works, it is problematic at slower speeds as torque is lost. So the hand crank gets used when cutting at very slow speeds (e.g., when making the final passes on a cut). Stepper motors provide a much better option as they maintain torque when running across the speed range used on the rose engine lathe. And, using stepper motors ensures a constant rotational speed at slower speeds, speeds measured in multiple minutes per revolution.

Do you sell a kit which accommodates multiple stepper motors?
The controls implemented will control the spindle stepper motor and one or two more at the same time. These are outlined in the user manual.

Can I get a different sized (or different amperage) stepper motor in my kit?
That is not an option we support at this time. The supplied kit is designed to work along known parameters. You are certainly welcome (and encouraged) to experiment.

Can I use a different sized (or different amperage) stepper motors?
That is not an option we support at this time. The supplied kit is designed to work along known parameters. You are certainly welcome (and encouraged) to experiment.

Can I get a different stepper motor controller or driver in my kit?
That is not an option we support at this time. The supplied kit is designed to work along known parameters. You are certainly welcome (and encouraged) to experiment.

Can I use a different stepper motor controller or driver?
The kit has been designed to easily utilize a very cost-effective approach to having a stepper motor drive the spindle. If you want to use a different controller or driver, you may, and are welcome to experiment.

To the extent that material may appear to be infringed, we assert that such alleged infringement is permissible under fair use principles in U.S. copyright laws. If you believe material has been used in an unauthorized manner, please contact me at ColvinTools@Gmail.com.

Portions of this document are copyrighted by Jon Magill and are used with his permission.

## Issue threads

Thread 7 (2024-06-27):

X Axis not Selected on Preferences Screen

RichColvin, 2024-06-27:
On the X Axis preferences screen, where one selects
- X Axis or
- Alt-X Axis

the X axis won't show as selected from the Nextion, though it does show as selected on the Teensy; i.e., the white box does stay selected but the gray one does.

Closed 2024-07-02.

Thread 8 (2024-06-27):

Keep Stepper Enabled won't stay selected

RichColvin, 2024-06-27:
On the Preferences More screen, Keep Steppers Enabled won't stay enabled on the Nextion side (i.e., the white box) but it does show enabled on the Teensy side (i.e., the gray box).

Closed 2024-07-02.

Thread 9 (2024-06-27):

SYNCHROnize of Spindle with M3 does not work as expected

RichColvin, 2024-06-27:
When on the MOVE screen,

1. Running the Spindle at 100% works as expected.
2. Running the M3 axis (using the rosette phaser/multiplier) at 100% works as expected.
3. Running the Spindle and M3 axes in Synchro mode does not work as expected.  The M3 runs at a much slower speed than the spindle, even though the Synchro is set at 100%.

RichColvin, 2024-07-02:
With version in 4.1.0b, works correctly for counter clockwise, but not for clockwise.  Copies of a picture of the EEPROM and videos of both CW & CCW are attached.

https://github.com/elfren/RoseEngine_SpindleAndAxis/assets/44912249/944b7404-4392-4cd7-bcf7-44834269bc17

https://github.com/elfren/RoseEngine_SpindleAndAxis/assets/44912249/05f287aa-64b2-4275-84ed-2f69e8ebb85a

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

RichColvin, 2024-07-02:
Found that the preference setting for the gear ratio on M3 was set to 30 rather than 9.  Don't know why it worked at before for one direction but not the other, but works now.

Closed 2024-07-02.

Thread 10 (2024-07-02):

Auxilliary pin does not work as expected

RichColvin, 2024-07-02:
Set aux pin to 26.  When engaging a function, the voltage does not get pulled down as expected.

RichColvin, 2024-07-02:
This was a user error:  the VCC for the relay was not plugged into the correct location on the PCB.

Closed 2024-07-02.

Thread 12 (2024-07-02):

MultiSync Program: Spindle

RichColvin, 2024-07-02:
When looking at the EEPROM, direction for Nextion vs. Teensy is always opposite.

- If CW is selected for the spindle, then Nextion shows CW, but Teensy shows CCW.
- If CCW is selected for the spindle, then Nextion shows CCW, but Teensy shows CW.

FYI:  M3 works as expected.

RichColvin, 2024-07-09:
Resolved in 4.1.0c

Closed 2024-07-09.

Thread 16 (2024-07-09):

Recip program (Spindle speed slider)

RichColvin, 2024-07-09:
This relates to version 4.1.0d

If the slider is changed from 95% to something else, it seems OK.  However when EEPROM is checked, Nextion shows the new % speed but Teensy shows 95%.  When going back to the Recip program screen, it is reset to 95% on the Nextion.

RichColvin, 2024-07-10:
Version 4.1.0e released.

Closed 2024-07-10.

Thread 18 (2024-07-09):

Sync Program

RichColvin, 2024-07-09:
Add a pause function to allow the user to pause, and then restart the activities.

This will be particularly useful for things such as fixing the cutting frame (e.g., if the secondary cable breaks).

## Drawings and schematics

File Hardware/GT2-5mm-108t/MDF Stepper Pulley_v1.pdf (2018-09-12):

# MDF Stepper Pulley

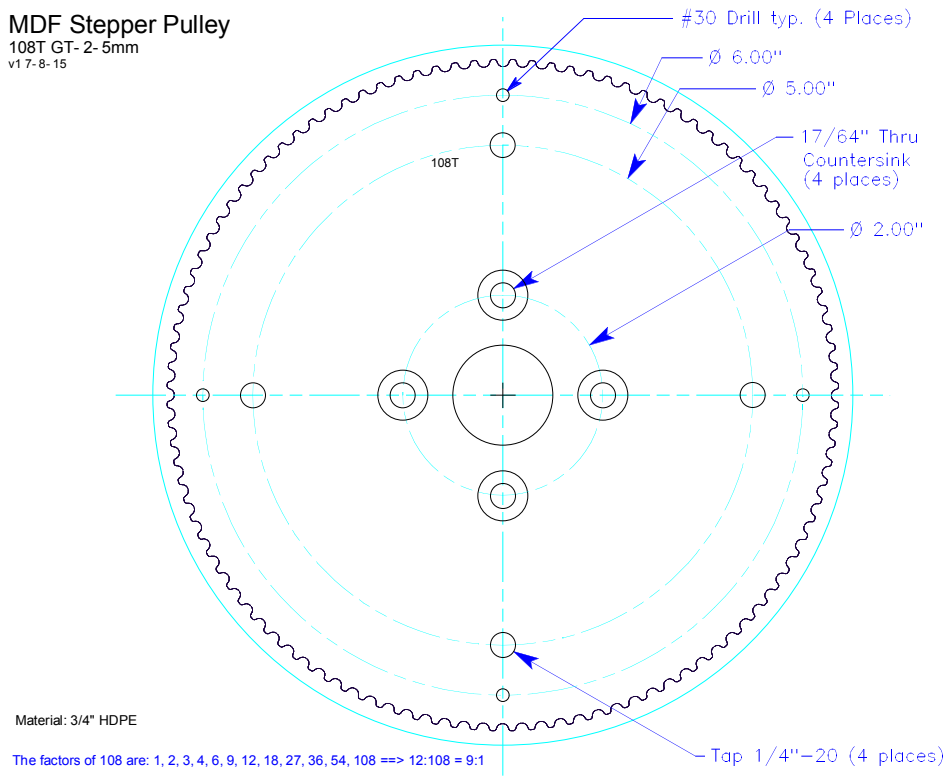
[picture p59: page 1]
Material: 3/4" HDPE

The factors of 108 are: 1, 2, 3, 4, 6, 9, 12, 18, 27, 36, 54, 108 ==> 12:108 = 9:1

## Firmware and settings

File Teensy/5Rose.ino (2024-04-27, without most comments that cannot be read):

#pragma once
/* *****************************************************************
* 5Rose main entry
* Author: Edward French
* Version: v3.1.1 - 4/24/24
******************************************************************/

#include "math.h"
#include <string>
#include <EEPROM.h>
//#include "C:\arduino\hardware\teensy\avr\libraries\EEPROM\EEPROM.h"
#include "5RoseDefines.h"
//#include "C:\arduino\hardware\teensy\avr\libraries\SD\src\SD.h"
#include <SD.h>
//#include "C:\arduino\hardware\teensy\avr\libraries\SPI\SPI.h"
#include <SPI.h>
#include <TeensyStep.h>

//#include "C:\arduino\hardware\teensy\avr\libraries\TeensyStep-master\src\TeensyStep.h" //  https://github.com/luni64/TeensyStep
//#include "C:\arduino\libraries\IniFile-master\src\IniFile.h" // https://github.com/stevemarple/IniFile
#include <IniFile.h>
//#include <MemoryFree.h>


//==================================================================
// Pin assignments:  See 5RoseDefines.h
//==================================================================
// TeensyStep  initialization
Stepper stepperSpindle(PIN_SPINDLE_STEP, PIN_SPINDLE_DIR);
Stepper stepperAxis_Z(PIN_AXIS_Z_STEP, PIN_AXIS_Z_DIR);
Stepper stepperAxis_X(PIN_AXIS_X_STEP, PIN_AXIS_X_DIR);
Stepper stepperAxis_M3(PIN_AXIS_3_STEP, PIN_AXIS_3_DIR);
Stepper stepperAxis_M4(PIN_AXIS_4_STEP, PIN_AXIS_4_DIR);

// TeensyStep controllers
RotateControl controllerAxis;
RotateControl controllerSpindle;

/// <summary>
/// Setup
/// </summary>
/// <comment>
/// Initial setup
/// </comment>
/// <returns></returns>
void setup()
{
	//const char* nextionEnd = "\xFF\xFF\xFF";
	pinMode(LED_BUILTIN, OUTPUT);

	// Initialize Serial0 (USB port) Baud rate is always at USB max.
	Serial.begin(115200);
	MilliDelay(15);
	uint32_t serialBaud = Serial.baud();

#ifdef DEBUG
	Serial.print("Baud:");
	Serial.println(serialBaud);
#endif // DEBUG

	SerialInitialize();
//
//	// Initialize Nextion LCD for 115200 baud and enable Serial1,2,or3.
//	// Note: Nextion requires 3 0xFF bytes to signal end of transmission
//	// Serial1
//
//	Serial1.begin(9600); //Nextion Serial baud rate set in Nextion pageMain Preinitialize Event tab
//	//Serial1.print("bauds=9600");
//	//Serial1.print(nextionEnd);
//	//MilliDelay(50);
//	//Serial1.print("bauds=9600");
//	//Serial1.print(nextionEnd);
//	//MilliDelay(50);
//
//	//Serial1.begin(921600); //Nextion Serial baud rate set in Nextion pageMain Preinitialize Event tab
//	Serial1.print("bauds=921600");
//	Serial1.print(nextionEnd);
//	MilliDelay(50);
//	Serial1.print("bauds=921600");
//	Serial1.print(nextionEnd);
//	MilliDelay(50);
//	Serial1.print("bkcmd=0");  // Set Nextion to return NO replies to each command
//	Serial1.print(nextionEnd);
//	MilliDelay(50);
//
//	if (Serial1.available() > 0)
//	{
//		serialId = 1;
//#ifdef DEBUG
//		Serial.print("1-serialId: ");
//		Serial.println(serialId);
//#endif // Debug
//	}
//	//	// Serial2
//	//	Serial2.begin(921600); //Nextion Serial baud rate set in Nextion pageMain Preinitialize Event tab
//	//	Serial2.print("bauds=921600");
//	//	Serial2.print(nextionEnd);
//	//	MilliDelay(50);
//	//	Serial2.print("bauds=921600");
//	//	Serial2.print(nextionEnd);
//	//	MilliDelay(50);
//	//	Serial2.print("bkcmd=0");  // Set Nextion to return NO replies to each command
//	//	Serial2.print(nextionEnd);
//	//	MilliDelay(50);
//	//	if (Serial2.available() > 0)
//	//	{
//	//		serialId = 2;
//	//#ifdef DEBUG
//	//		Serial.print("2-serialId: ");
//	//		Serial.println(serialId);
//	//#endif // Debug
//	//	}
//
//		// Serial3
//		//Serial3.begin(115200); //Nextion Serial baud rate set in Nextion pageMain Preinitialize Event tab
//	Serial3.begin(921600); //Nextion Serial baud rate set in Nextion pageMain Preinitialize Event tab
//	//Serial3.print("bauds=115200");
//	Serial3.print("bauds=921600");
//	Serial3.print(nextionEnd);
//	MilliDelay(50);
//	//Serial3.print("bauds=115200");
//	Serial3.print("bauds=921600");
//	Serial3.print(nextionEnd);
//	MilliDelay(50);
//	Serial3.print("bkcmd=0");  // Set Nextion to return NO replies to each command
//	Serial3.print(nextionEnd);
//	MilliDelay(50);
//	if (Serial3.available() > 0)
//	{
//		serialId = 3;
//#ifdef DEBUG
//		Serial.print("3-serialId: ");
//		Serial.println(serialId);
//#endif // Debug
//	}

	// Serial4
#ifndef TEENSY_32
	Serial4.begin(921600); //Nextion Serial baud rate set in Nextion pageMain Preinitialize Event tab
	Serial4.print("bauds=921600");
	Serial4.print(nextionEnd);
	MilliDelay(50);
	//Serial3.print("bauds=115200");
	Serial4.print("bauds=921600");
	Serial4.print(nextionEnd);
	MilliDelay(50);
	Serial4.print("bkcmd=0");  // Set Nextion to return NO replies to each command
	Serial4.print(nextionEnd);
	MilliDelay(50);

	if (Serial4.available() > 0)
	{
		serialId = 4;
#ifdef DEBUG
		Serial.print("4-serialId: ");
		Serial.println(serialId);
#endif // Debug
	}
#endif //Teensy_32


#ifdef DEBUG
	Serial.print("serialId: ");
	Serial.println(serialId);
#endif // Debug
	//Update with values from EEProm
	EEPROM.get(eePromAddress_Setup, configSetup);
	EEPROM.get(eePromAddress_Main, configMain);
#ifdef DEBUG
	Serial.print("                                eePromAddress_Main: ");
	Serial.println(eePromAddress_Main);
#endif // DEBUG
	EEPROM.get(eePromAddress_Sync, configSync);

	EEPROM.get(eePromAddress_Multi, configMulti);
	EEPROM.get(eePromAddress_Ind_Prime, configIndex_Prime);
	EEPROM.get(eePromAddress_Ind_1, configIndex_1);
	EEPROM.get(eePromAddress_Ind_2, configIndex_2);
	EEPROM.get(eePromAddress_Ind_3, configIndex_3);
	EEPROM.get(eePromAddress_Ind_4, configIndex_4);
	EEPROM.get(eePromAddress_Ind_5, configIndex_5);
	EEPROM.get(eePromAddress_Mov, configMove);
	EEPROM.get(eePromAddress_Rose, configRose);
	EEPROM.get(eePromAddress_Rec, configRec);
	EEPROM.get(eePromAddress_Grk, configGreekKey);

#ifdef DEBUG
	Serial.print("configMain.axisId: ");
	Serial.println(configMain.axisId);
	Serial.print("configOne.axisId: ");
	Serial.println(configMulti.axisId);
	Serial.print("configIndex_Main.indexId: ");
	Serial.println(configIndex_Prime.indexId);
	Serial.print("configMove.axisId: ");
	Serial.println(configMove.axisId);
	Serial.print("configSync.axisId: ");
	Serial.println(configSync.axisId);
	Serial.print("configRec.axisId: ");
	Serial.println(configRec.axisId);
	Serial.print("configGreekKey.axisId: ");
	Serial.println(configGreekKey.axisId);
	Serial.print("configRose.axisId: ");
	Serial.println(configRose.axisId);
#endif // DEBUG



	// Config as well as all other EEProm settings should be run from Nextion whenever Teensy is updated.  
	// EEProm may contain invalid settings otherwise.


// Enable SD card reader
// 
//  Note: Only pins 9 and 10 are supported
	pinMode(PIN_SPI_CS_10, OUTPUT);
	digitalWrite(PIN_SPI_CS_10, HIGH);

	pinMode(PIN_SPI_CS_9, OUTPUT);
	digitalWrite(PIN_SPI_CS_9, HIGH);

	// Start SD
	BeginSD();

	pinMode(PIN_SPINDLE_ENABLE, OUTPUT);
	pinMode(PIN_AXIS_Z_ENABLE, OUTPUT);

	pinMode(PIN_AXIS_X_ENABLE, OUTPUT);
	pinMode(PIN_AXIS_3_ENABLE, OUTPUT);


	SetEnable(ID_SPINDLE, false, true);
	SetEnable(ID_AXIS_Z, false, true);
	SetEnable(ID_AXIS_X, false, true);
	SetEnable(ID_AXIS_3, false, true);

	//motorCount = configSetup.motorCount;
	//vendorId = configSetup.vendorId;
	//motorCount = 5;
	//vendorId = 4;



	if (configSetup.motorCount == 5)
	{
		pinMode(PIN_AXIS_4_ENABLE, OUTPUT);
		SetEnable(ID_AXIS_4, false, true);

		if (configSetup.limit_Min_M4 > 9 && configSetup.limit_Min_M4 < 40)
		{
			pinMode(configSetup.limit_Min_M4, INPUT_PULLUP);
			MilliDelay(10);
			digitalWrite(configSetup.limit_Min_M4, configSetup.limit_NCorNO);  // Enable
		}
		if (configSetup.limit_Max_M4 > 9 && configSetup.limit_Max_M4 < 40)
		{
			pinMode(configSetup.limit_Max_M4, INPUT_PULLUP);
			MilliDelay(10);
			digitalWrite(configSetup.limit_Max_M4, configSetup.limit_NCorNO);  // Enable
		}

	}
	else
	{
		digitalWriteFast(PIN_AXIS_4_ENABLE, LOW);
	}

	// Initialize Limit switches	
	if (configSetup.limit_Min_Z > 9 && configSetup.limit_Min_Z < 40)
	{
		pinMode(configSetup.limit_Min_Z, INPUT_PULLUP);
		MilliDelay(10);
		digitalWrite(configSetup.limit_Min_Z, configSetup.limit_NCorNO);  // Enable
	}
	if (configSetup.limit_Max_Z > 9 && configSetup.limit_Max_Z < 40)
	{
		pinMode(configSetup.limit_Max_Z, INPUT_PULLUP);
		MilliDelay(10);
		digitalWrite(configSetup.limit_Max_Z, configSetup.limit_NCorNO);  // Enable
	}

	if (configSetup.limit_Min_X > 9)
	{
		pinMode(configSetup.limit_Min_X, INPUT_PULLUP);
		MilliDelay(10);
		digitalWrite(configSetup.limit_Min_X, configSetup.limit_NCorNO);  // Enable
	}
	if (configSetup.limit_Max_X > 9)
	{
		pinMode(configSetup.limit_Max_X, INPUT_PULLUP);
		MilliDelay(10);
		digitalWrite(configSetup.limit_Max_X, configSetup.limit_NCorNO);  // Enable
	}

	if (configSetup.limit_Min_M3 > 9)
	{
		pinMode(configSetup.limit_Min_M3, INPUT_PULLUP);
		MilliDelay(10);
		digitalWrite(configSetup.limit_Min_M3, configSetup.limit_NCorNO);  // Enable
	}
	if (configSetup.limit_Max_M3 > 9)
	{
		pinMode(configSetup.limit_Max_M3, INPUT_PULLUP);
		MilliDelay(10);
		digitalWrite(configSetup.limit_Max_M3, configSetup.limit_NCorNO);  // Enable
	}

	if (configSetup.auxillaryPin > 9 && configSetup.auxillaryPin < 40)
	{
		pinMode(configSetup.auxillaryPin, OUTPUT);
		digitalWrite(configSetup.auxillaryPin, HIGH);  // Enable
		uint8_t auxState = digitalRead(configSetup.auxillaryPin);
		Serial.print("auxState: ");
		Serial.println(auxState);
	}
	else
	{
		Serial.println("auxillaryPin not enabled");
	}

	MilliDelay(10);

	if (configSetup.eStop > 9 && configSetup.eStop < 40)
	{
		pinMode(configSetup.eStop, INPUT_PULLUP);
		digitalWrite(configSetup.eStop, configSetup.limit_NCorNO);  // Enable
	}

	MilliDelay(10);

	SetEnable(ID_SPINDLE, false, true);

#ifndef TEENSY_32
	for (int i = 0; i < 3; i++) // Verify Teensy is operational
	{
		digitalWrite(LED_BUILTIN, HIGH);
		MilliDelay(50);
		digitalWrite(LED_BUILTIN, LOW);
		MilliDelay(300);
	}
#endif // !TEENSY_32

	// Set Spindle and M3 Synchro ratio
	synchro_Ratio = configSetup.gearRatio_AxisM3 / configSetup.gearRatio_Spindle;

#ifdef VERBOSE
	Serial.print("configSetup.gearRatio_Spindle: ");
	Serial.println(configSetup.gearRatio_Spindle, 5);
	Serial.print("configSetup.gearRatio_AxisM3: ");
	Serial.println(configSetup.gearRatio_AxisM3, 5);

	Serial.print("synchro_Ratio: ");
	Serial.println(synchro_Ratio, 5);
#endif // VERBOSE

#ifdef DEBUG
	const char* initialized = "Initialized...";
	Serial.println(initialized);
#endif // DEBUG

	// Uncomment to get size of defined structs.
	StructSizeCalc();
}

/// <summary>
/// Loop
/// </summary>
/// <comment>
/// Main program loop
/// </comment>
/// <returns></returns>
void loop()
{
	const char* pageCallerId_Char = "Page Caller ID:  ";

	const char* steps360_Char = "Steps/360: ";
	const char* gearRatio_Char = "Gear Ratio: ";
	const char* maxSpd_Char = "MaxSpeed:  ";
	const char* accel_Char = "Accel:  ";
	const char* polarity_Char = "Polarity:  ";
	const char* distance_Char = "Distance:  ";

	const char* axisId_Char = "Axis ID:  ";
	const char* indexId_Char = "Index ID:  ";
	const char* z_LimitMin_Char = "Limit Min Z:  ";
	const char* z_LimitMax_Char = "Limit Max Z:  ";

	const char* x_LimitMin_Char = "Limit Min X:  ";
	const char* x_LimitMax_Char = "Limit Max X:  ";

	const char* m3_LimitMin_Char = "Limit Min M3:  ";
	const char* m3_LimitMax_Char = "Limit Max M3:  ";

	const char* m4_LimitMin_Char = "Limit Min M4:  ";
	const char* m4_LimitMax_Char = "Limit Max M4:  ";

	const char* index1_Char = "Index1:  ";
	const char* index2_Char = "Index2:  ";
	const char* index3_Char = "Index3:  ";
	const char* index4_Char = "Index4:  ";
	const char* index5_Char = "Index5:  ";

	const char* degreeDivision_Char = " Degree or Division:  ";
	const char* radialOrAxial_Char = "Radial or Axial:  ";
	const char* helixType_Char = "Helix Type:  ";
	const char* amplitude_Char = "Amplitude:  ";
	const char* revolutions_Char = "Revolutions:  ";
	const char* waveDir_Char = "Wave Direction:  ";
	const char* waves_Char = "Waves:  ";
	const char* degrees_Char = "Degrees:  ";
	const char* segmentActual_Char = "Segment or Actual:  ";
	const char* segmentLength_Char = "Segment Length:  ";
	const char* patternCount_Char = "Pattern Count:  ";
	const char* pattern_Char = "Pattern:  ";
	const char* reverseDirection_Char = "Reverse Direction:  ";
	const char* fileOrFixed_Char = " File or Fixed:  ";

	const char* rose_D_Char = "d: ";
	const char* rose_N_Char = "n: ";

	if (Serial1.available() > 0)
	{
		serialId = 1;
#ifdef DEBUG
		Serial.print("1.serialId: ");
#endif // Debug
	}
	//	else if (Serial2.available() > 0)
	//	{
	//		serialId = 2;
	//#ifdef DEBUG
	//		Serial.print("2.serialId: ");
	//#endif // Debug
	//	}
	else if (Serial3.available() > 0)
	{
		serialId = 3;
#ifdef DEBUG
		Serial.print("3.serialId: ");
#endif // Debug
	}
#ifndef TEENSY_32
	else if (Serial4.available() > 0)
	{
		serialId = 4;
#ifdef DEBUG
		Serial.print("3.serialId: ");
#endif // Debug
	}
#endif //Teensy_32

	// All Nextion incoming data packets are terminated with one 0xFF byte

	int serialPortAvailable = 0;
	if ((Serial1.available() > 0) || (Serial3.available() > 0))
	{
		serialPortAvailable = 1;
	}
#ifndef TEENSY_32
	else if (Serial4.available() > 0)
	{

		serialPortAvailable = 1;
	}
#endif // Teensy 32

	if (serialPortAvailable > 0)
	{
		incomingByte = SerialRead(serialId);

#ifdef DEBUG
		Serial.print("serialId: ");
		Serial.println(serialId);
#endif // DEBUG

		// Allow processing time for serial data
		MilliDelay(15);


		switch (incomingByte)
		{
			//case 33 through 42: Not Used.
			//{
			//	break;
			//}
		case 41: // ) - Not Used
		{

			break;
		}
		case 42: // * - 
		{

			break;
		}
		case 43: // + - Greek Key: Pattern radial or axial
		{
			configGreekKey.radialOrAxial_Pattern = GetSerialInteger();
			EEPROM.put(eePromAddress_Grk, configGreekKey);
			break;
		}
		case 44: // , - Greek Key: File radial or axial
		{
			configGreekKey.radialOrAxial_File = GetSerialInteger();
			EEPROM.put(eePromAddress_Grk, configGreekKey);
			break;
		}
		case 45: // - - Not Used
		{
			break;
		}
		case 46: // . - Greek Key: Pattern count(pattern repeats)
		{
			configGreekKey.patternCount_Pattern = GetSerialInteger();
			EEPROM.put(eePromAddress_Grk, configGreekKey);
			break;
		}
		//case 47 - 57: Don't Use
			//{
			//	break;
			//}
		case 58: // : Colon - Spindle MaxSpeed
		{
			int maxSpeed_Spindle = (int)GetSerialFloat(serialId);
#ifdef DEBUG
			const char* pageCallerId_Char = "pageCallerId:";
			Serial.print(pageCallerId_Char);
			Serial.println(pageCallerId);
#endif // DEBUG
			switch (pageCallerId)
			{
			case PAGE_MAIN:
			{

				configMain.maxSpd_Spindle = maxSpeed_Spindle;
				EEPROM.put(eePromAddress_Main, configMain);
#ifdef DEBUG
				Serial.print(maxSpd_Char);
				Serial.println(configMain.maxSpd_Spindle);
#endif // DEBUG
				break;
			}
			case PAGE_MULTI:
			case PAGE_ONE:
			{
				configMulti.maxSpd_Spindle = maxSpeed_Spindle;
				EEPROM.put(eePromAddress_Multi, configMulti);

				break;
			}
			case PAGE_INDEX:
			{
				configIndex_Prime.maxSpd_Spindle = maxSpeed_Spindle;
				EEPROM.put(eePromAddress_Ind_Prime, configIndex_Prime);
#ifdef DEBUG
				Serial.print(maxSpd_Char);
				Serial.println(configIndex_Prime.maxSpd_Spindle);
#endif // DEBUG
				break;
			}
			case PAGE_SYNC:
			case PAGE_REC:
			case PAGE_GRK:
			case PAGE_PROGRAM:
			{
				configSync.maxSpd_Spindle = maxSpeed_Spindle;
				configRec.maxSpd_Spindle = maxSpeed_Spindle;
				configGreekKey.maxSpd_Spindle = maxSpeed_Spindle;

				EEPROM.put(eePromAddress_Sync, configSync);
				EEPROM.put(eePromAddress_Rec, configRec);
				EEPROM.put(eePromAddress_Grk, configGreekKey);
#ifdef DEBUG
				Serial.print(maxSpd_Char);
				Serial.println(configSync.maxSpd_Spindle);
#endif // DEBUG
				break;
			}
			case PAGE_ROSE:
			{
				configRose.maxSpd_Spindle = maxSpeed_Spindle;
				EEPROM.put(eePromAddress_Rose, configRose);
#ifdef DEBUG
				Serial.print(maxSpd_Char);
				Serial.println(configRose.maxSpd_Spindle);
#endif // DEBUG
				break;
			}
			}
			break;
		}
		case 59: // ; Semicolon - Spindle Acceleration
		{
			int spindleAccel = (int)GetSerialFloat(serialId);
			switch (pageCallerId)
			{
			case PAGE_MAIN:
			{
				configMain.accel_Spindle = spindleAccel;
				EEPROM.put(eePromAddress_Main, configMain);
#ifdef DEBUG
				Serial.print(accel_Char);
				Serial.println(configMain.accel_Spindle);
#endif // DEBUG
				break;
			}
			case PAGE_MULTI:
			case PAGE_ONE:
			{

				configMulti.accel_Spindle = spindleAccel;
#ifdef DEBUG
				Serial.print(accel_Char);
				Serial.println(configMulti.accel_Spindle);
#endif // DEBUG
				EEPROM.put(eePromAddress_Multi, configMulti);
				break;
			}
			case PAGE_INDEX:
			{
				configIndex_Prime.accel_Spindle = spindleAccel;
				EEPROM.put(eePromAddress_Ind_Prime, configIndex_Prime);
#ifdef DEBUG
				Serial.print(accel_Char);
				Serial.println(configIndex_Prime.accel_Spindle);
#endif // DEBUG
				break;
			}
			case PAGE_SYNC:
			case PAGE_REC:
			case PAGE_GRK:
			case PAGE_PROGRAM:
			{
				configSync.accel_Spindle = spindleAccel;
				configRec.accel_Spindle = spindleAccel;
				configGreekKey.accel_Spindle = spindleAccel;

				EEPROM.put(eePromAddress_Sync, configSync);
				EEPROM.put(eePromAddress_Rec, configRec);
				EEPROM.put(eePromAddress_Grk, configGreekKey);
#ifdef DEBUG
				Serial.print(accel_Char);
				Serial.println(configSync.accel_Spindle);
#endif // DEBUG
				break;
			}
			case PAGE_ROSE:
			{
				configRose.accel_Spindle = spindleAccel;
				EEPROM.put(eePromAddress_Rose, configRose);
#ifdef DEBUG
				Serial.print(accel_Char);
				Serial.println(configRose.accel_Spindle);
#endif // DEBUG
				break;
			}
			} // end switch (pageCallerId)

			break;
		}
		case 60: // < Less than - Not Used
		{
			break;
		}
		case 61: // = Do pageProgram CCW
		{
			GetFilenameFromSerial();
			Program_FromFile(DIR_CCW);

			break;
		}
		case 62: // > Greater than - Do pageProgram CW
		{
			GetFilenameFromSerial();
			Program_FromFile(DIR_CW);
			break;
		}
		case 63: // ? Question mark - pageRec Retro Spindle Change
		{
			configRec.retro_SpindleChange = GetSerialFloat(serialId);
			EEPROM.put(eePromAddress_Rec, configRec);
#ifdef DEBUG
			Serial.print("configRec.retro_SpindleChange");
			Serial.println(configRec.retro_SpindleChange, 5);
#endif // DEBUG
			break;
		}
		case 64: // @ - Restart microSD port
		{
			Serial.println("Restart microSD port");
			lastFileIndex = -1;
			currentFileIndex = 0;
			BeginSD();
			break;
		}
		case 65: // A - Load Settings.ini
		{
			iniFileType = INI_4AXES;
			GetFilenameFromSerial();
			LoadSettings();
			break;
		}
		case 66: //B - AxisId
		{
			int axisId = GetSerialInteger();

			Serial.print("                   1234             pageCallerId:  ");
			Serial.println(pageCallerId);
			Serial.print("1.axisId:  ");
			Serial.println(axisId);
			switch (pageCallerId)
			{
			case PAGE_MAIN:
			{
				configMain.axisId = axisId;

				EEPROM.put(eePromAddress_Main, configMain);
				uint32_t myVal = 15;
#ifdef DEBUG

				Serial.print("              567                   configMain.axisId:  ");
				Serial.println(configMain.axisId);

				EEPROM.get(600, myVal);
				Serial.print("maxSpd_Spindle--600:  ");
				Serial.println(myVal);

				EEPROM.get(604, myVal);
				Serial.print("maxSpd_Axis_Z--604:  ");
				Serial.println(myVal);

				EEPROM.get(608, myVal);
				Serial.print("maxSpd_Axis_X--608:  ");
				Serial.println(myVal);

				EEPROM.get(612, myVal);
				Serial.print("maxSpd_Axis_M3--612:  ");
				Serial.println(myVal);

				EEPROM.get(616, myVal);
				Serial.print("maxSpd_Axis_M4--616:  ");
				Serial.println(myVal);


				EEPROM.get(672, myVal);
				Serial.print("myVal--AxisId:  ");
				Serial.println(myVal);
#endif // DEBUG
				break;
			}
			case PAGE_MULTI:
			case PAGE_ONE:
			{
				Serial.print("2.axisId:  ");
				Serial.print(configMulti.axisId);
				configMulti.axisId = axisId;
				EEPROM.put(eePromAddress_Multi, configMulti);

				Serial.print("   3.axisId:  ");
				Serial.println(configMulti.axisId);
				break;
			}
			case PAGE_INDEX:
			{
				configIndex_Prime.axisId = axisId;
#ifdef DEBUG
				Serial.print("Index axisId:  ");
				Serial.println(configIndex_Prime.axisId);
#endif // DEBUG
				EEPROM.put(eePromAddress_Ind_Prime, configIndex_Prime);
				break;
			}
			case PAGE_MOVE:
			{
				configMove.axisId = axisId;
				EEPROM.put(eePromAddress_Mov, configMove);
				break;
			}
			case PAGE_BE:
			{
				break;
			}
			case PAGE_SYNC:
			case PAGE_REC:
			case PAGE_GRK:
			case PAGE_PROGRAM:
			{
				configSync.axisId = axisId;
				configRec.axisId = axisId;
				configGreekKey.axisId = axisId;
				//configMove.axisId = axisId;

				EEPROM.put(eePromAddress_Sync, configSync);
				EEPROM.put(eePromAddress_Rec, configRec);
				EEPROM.put(eePromAddress_Grk, configGreekKey);
				//EEPROM.put(eePromAddress_Mov, configMove);
#ifdef DEBUG
				Serial.print(axisId_Char);
				Serial.println(configSync.axisId);
#endif // DEBUG
				break;
			}

			case PAGE_ROSE:
			{
				configRose.axisId = axisId;
				EEPROM.put(eePromAddress_Rose, configRose);
				break;
			}


			}
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

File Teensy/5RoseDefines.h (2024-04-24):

/* *****************************************************************
* Rose Engine Spindle definitions
* Author: Edward French
******************************************************************/
#pragma once
//#define SHOW_POSITION
#define DEBUG
#define VERBOSE
#define TEENSY_32
#define ESTOP_ENABLED
//==================================================================
// Pin assignments
//==================================================================

//// Spindle
#define ID_SPINDLE 0  
#define PIN_SPINDLE_DIR 2  //Stepper direction
#define PIN_SPINDLE_STEP 3  //Stepper step
#define PIN_SPINDLE_ENABLE 4 //Enable

// Z axis
#define ID_AXIS_Z 1
#define PIN_AXIS_Z_DIR 5 // Stepper direction
#define PIN_AXIS_Z_STEP 6 // Stepper step
#define PIN_AXIS_Z_ENABLE 14 // Enable 


// X axis
#define ID_AXIS_X 2
#define PIN_AXIS_X_DIR 20  // Stepper direction
#define PIN_AXIS_X_STEP 21 // Stepper step
#define PIN_AXIS_X_ENABLE 22 // Enable 

// M3 axis
#define ID_AXIS_3 3
#define PIN_AXIS_3_DIR 23  // Stepper direction
#define PIN_AXIS_3_STEP 16  // Stepper step
#define PIN_AXIS_3_ENABLE 17 // Enable 

// M4 axis
#define ID_AXIS_4 4
#define PIN_AXIS_4_DIR 19  // Stepper direction
#define PIN_AXIS_4_STEP 18  // Stepper step
#define PIN_AXIS_4_ENABLE 15 // Enable 

/////////////////////////////////////////////////////////////////////////
// Constants
/////////////////////////////////////////////////////////////////////////

#define MIN_SPEED 250

// Move page
#define ID_MOVE_AXIS_Z1 1
#define ID_MOVE_AXIS_Z2 11
#define ID_MOVE_AXIS_X1 2
#define ID_MOVE_AXIS_X2 12
#define ID_MOVE_AXIS_M3_1 3
#define ID_MOVE_AXIS_M3_2 13

#define ID_MOVE_AXIS_M4_1 4
#define ID_MOVE_AXIS_M4_2 14

// SPI
#define PIN_SPI_CS_10 10  // Primary pin for SPI
#define PIN_SPI_CS_9 9

#define PIN_SPI_CS_15 15
#define PIN_SPI_CS_24 24

// Index page ID
#define ID_INDEX_1 1
#define ID_INDEX_2 2
#define ID_INDEX_3 3
#define ID_INDEX_4 4
#define ID_INDEX_5 5

#define DIR_CCW (-1)

#define DIR_CW 1

#define RETURN_SPINDLE 1
#define RETURN_SPINDLE_M3 2
#define RETURN_AXIS 3

#define BY_DEGREES 1 
#define BY_DIVISIONS 0

#define FIXED 0
#define FILE_SD 1

#define INCHES 0
#define MILLIMETERS 1

#define WAVE_IN -1
#define WAVE_OUT 1

#define RADIAL 0
#define AXIAL 1
#define RADIAL_M3 0
#define LINEAR_M3 1
#define RADIAL_M4 0
#define LINEAR_M4 1

#define INI_4AXES 0
#define INI_RESET 1

#define TRIANGLE_STYLE 1
#define SQUARE_STYLE 2
#define SAWTOOTH_STYLE 3

#define INDEX_1 1
#define INDEX_2 2
#define INDEX_3 3
#define INDEX_4 4
#define INDEX_5 5
/////////////////////////////////////////////////////////////////////////
// Page defines
/////////////////////////////////////////////////////////////////////////
#define PAGE_SPLASH 0
#define PAGE_MAIN 1
#define PAGE_ONE 2
#define PAGE_INDEX 3
#define PAGE_MOVE 4
#define PAGE_BE 5
#define PAGE_SYNC 6
#define PAGE_REC 7
#define PAGE_GRK 8
#define PAGE_PROGRAM 9
#define PAGE_ROSE 10 
#define PAGE_MULTI 11 
#define PAGE_GEO 12
#define PAGE_NUMBERPAD 13 
#define PAGE_SPINDLE 14
#define PAGE_Z 15
#define PAGE_X 16
#define PAGE_ALTERNATEX 17
#define PAGE_MOTOR_3 18
#define PAGE_MOTOR_4 19
#define PAGE_LIMITS 20
#define PAGE_RETURNS 21
#define PAGE_MORE 22
#define PAGE_FILELIST 23
#define PAGE_EEPROM 24
#define PAGE_ERROR 25
#define PAGE_INI 26

/////////////////////////////////////////////////////////////////////////
// Structs
/////////////////////////////////////////////////////////////////////////

struct nextionData
{
	uint8_t value24;
	uint8_t value16;
	uint8_t value08;
	uint8_t value00;
};

struct nextionData2
{
	uint8_t value00;
	uint8_t value08;
	uint8_t value16;
	uint8_t value24;
};


struct configPageMov
{
	uint32_t axisId;
	uint32_t maxSpd_Axis_Z;
	uint32_t accel_Axis_Z;
	uint32_t speedPercent_Axis_Z;
	uint32_t maxSpd_Axis_X;
	uint32_t accel_Axis_X;
	uint32_t speedPercent_Axis_X;
	uint32_t maxSpd_Motor_3;
	uint32_t accel_Motor_3;
	uint32_t speedPercent_Axis_M3;
	uint32_t maxSpd_Motor_4;
	uint32_t accel_Motor_4;
	uint32_t speedPercent_Axis_M4;
	float distance_MoveZ1;
	float distance_MoveX1;
	float distance_MoveM3_1;
	float distance_MoveM4_1;
	float distance_MoveZ2;
	float distance_MoveX2;
	float distance_MoveM3_2;
	float distance_MoveM4_2;
};

struct configPageSync
{
	uint32_t axisId;
	uint32_t maxSpd_Spindle;
	uint32_t accel_Spindle;
	uint32_t maxSpd_Axis_Z;
	uint32_t accel_Axis_Z;
	uint32_t maxSpd_Axis_X;
	uint32_t accel_Axis_X;
	uint32_t maxSpd_Axis_M3;
	uint32_t accel_Axis_M3;
	uint32_t maxSpd_Axis_M4;
	uint32_t accel_Axis_M4;
	uint32_t speedPercent_Spindle;
	uint32_t speedPercent_Axis_Z;
	uint32_t speedPercent_Axis_X;
	uint32_t speedPercent_Axis_M3;
	uint32_t speedPercent_Axis_M4;
	uint32_t helixType;
	uint32_t spindle_RevolutionsOrDegrees;
	float distance;
	float revolutions_Spindle;
};
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

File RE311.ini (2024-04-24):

; Rose Engine Ini file
; V3.0
[Preferences]
;
;More
VendorId=4
MotorCount=5
;CutterMotorPin must be greater than 16 on 4 motor board.
;CutterMotorPin must be greater than 24 on 5 motor board.
Auxillary Pin=47
KeepSteppersEnabled=0
; Spindle
Microsteps_Spindle=32
StepsPer360_Spindle=200
GearRatio_Spindle=9
;Polarity: Low=1, High=0
Polarity_Spindle=1
;Z Axis
Microsteps_Z=32
StepsPer360_Z=200
DistancePer360_Z=0.187
Polarity_Z=1
; Hand: 0=Left, 1=Right
Leadscrew_Hand_Z=0
;X Axis
XorAltXSelected=0
Microsteps_X=32
StepsPer360_X=200
DistancePer360_X=0.187
Polarity_X=1
Leadscrew_Hand_X=0
;Alternate X Axis
Microsteps_AltX=32
StepsPer360_AltX=200
DistancePer360_AltX=0.283
Polarity_AltX=1
Leadscrew_Hand_AltX=1
;M3 Axis
Microsteps_M3=32
StepsPer360_M3=200
GearRatio_M3=30
Polarity_M3=1
DistancePer360_M3=1.02354
RadialOrLineal_M3=0
M3Radius=5.124
Leadscrew_Hand_M3=1
;M4 Axis
Microsteps_M4=32
StepsPer360_M4=200
GearRatio_M4=30
Polarity_M4=1
DistancePer360_M4=0.0254
RadialOrLineal_M4=1
M4Radius=11.258
Leadscrew_Hand_M4=1
;
[Limits]
;
;Limit Switches and Stop pins must be greater than 16 on 4 motor board.
;Limit Switches and Stop pins must be greater than 24 on 5 motor board.
Min_Z=24
Max_Z=26
Min_X=24
Max_X=26
Min_M3=24
Max_M3=26
Min_M4=24
Max_M4=26
;Stop spindle when limit hit = 0.  Leave spindle running =1
StopSpindle=0
Stop=28
;Normally Closed=0, Normally Open=1
NC-NO=1
;
[Returns]
;
;Return
; All speeds and accellerations are in steps per second
MaxSpeed_Spindle=30000
Accel_Spindle=20000
MaxSpeed_Axis_Z=30000
Accel_Axis_Z=20000
MaxSpeed_Axis_X=30000
Accel_Axis_X=20000
MaxSpeed_Axis_M3=30000
Accel_Axis_M3=20000
MaxSpeed_Axis_M4=30000
Accel_Axis_M4=20000
;
[Main]
;
;Axis Ids:
;-----------------
;Z=1
;X=2
;M3=3
;M4=4
;Spindle=0
;-----------------
AxisId=1
;Spindle
MaxSpeed_Spindle=15000
Accel_Spindle=20000
SpeedPercentage_Spindle=51
;Z Axis
MaxSpeed_Z=15000
Accel_Z=20000
SpeedPercentage_Z=53
;X Axis
MaxSpeed_X=4000
Accel_X=20000
SpeedPercentage_X=54
;M3 Axis
MaxSpeed_M3 =5007
Accel_M3 =20000
SpeedPercentage_M3 =59
;M4 Axis
MaxSpeed_M4 =5007
Accel_M4 =20000
SpeedPercentage_M4 =60
;
[One_Multi]
;
; Settings are shared between One and Multi pages.
AxisId=1
; MultiAxesRun and Direction values are ANDed together.
MultiAxesIDs=0
;Spindle
MaxSpeed_Spindle=2500
Accel_Spindle=20000
SpeedPercentage_Spindle=61
TargetDistance_Spindle=39.45
; CW=2, CCW=3
Direction_Spindle=2
;Z Axis
MaxSpeed_Z=5062
Accel_Z=20000
SpeedPercentage_Z=64
TargetDistance_Z=2.123
; Right=2, Left=3
Direction_Z=2
;X Axis
MaxSpeed_X=5065
Accel_X=20000
SpeedPercentage_X=67
TargetDistance_X=3.514
; Right=2, Left=3
Direction_X=3
;M3 Axis
MaxSpeed_M3=5068
Accel_M3=20000
SpeedPercentage_M3=70
TargetDistance_M3=1.369
; Right and CW=2, Left and CCW=3
Direction_M3=2
;M4 Axis
MaxSpeed_M4=5068
Accel_M4=20000
SpeedPercentage_M4=70
TargetDistance_M4=0.478
; Right and CW=2, Left and CCW=3
Direction_M4=3
;
[Index]
;
;Axis Ids:
;-----------------
;M3=3
;M4=4
;Spindle=0
;-----------------
AxisId=0
IndexId=1
; Spindle
MaxSpeed_Spindle=5070
Accel_Spindle=20000
SpeedPercentage_Spindle=72
; M3
MaxSpeed_M3=5072
Accel_M3=20000
SpeedPercentage_M3=73
; M4
MaxSpeed_M4=5072
Accel_M4=20000
SpeedPercentage_M4=85
;-----------------
;Division:0  Degrees:1
;Fixed:0  File:1
;-----------------
;Index 1
DivisionsOrDegrees_1=1
FixedOrFile_1=0
Size_1=60.35
;Index 2
DivisionsOrDegrees_2=1
FixedOrFile_2=0
Size_2=22.5
;Index 3
DivisionsOrDegrees_3=1
FixedOrFile_3=0
Size_3=11.24
;Index 4
DivisionsOrDegrees_4=0
FixedOrFile_4=0
Size_4=180
;Index 5
DivisionsOrDegrees_5=0
FixedOrFile_5=0
Size_5=45
;Synchronize M3 and Spindle
Synchro_M3_and_Spindle=0
Synchro_Percentage=100
;
[Move]
;
AxisId=1
;Z Axis
MaxSpeed_Z=5080
Accel_Z=20000
SpeedPercentage_Z=82
Distance_Z1=4.125
Distance_Z2=3.1
;X Axis
MaxSpeed_X=5083
Accel_X=20000
SpeedPercentage_X=85
Distance_X1=5.75
Distance_X2=5.76
;M3 Axis
MaxSpeed_M3=5086
Accel_M3=20000
SpeedPercentage_M3=88
Distance_M3-1=5.78
Distance_M3-2=5.79
;M4 Axis
MaxSpeed_M4=5088
Accel_M4=20000
SpeedPercentage_M4=89
Distance_M4-1=4.78
Distance_M4-2=4.79
;
[Shared]
;
; Settings shared between Main,Sync, Recip, Rose, Greek Key, and Program pages
;Synchronize M3 and Spindle
Synchro_M3_and_Spindle=0
Synchro_Percentage=100
; Settings shared between Sync, Recip, Greek Key, and Program pages
AxisId=1
RadialOrAxial=0
;Spindle
MaxSpeed_Spindle=5040
Accel_Spindle=20000
SpeedPercentage_Spindle=42
;Z Axis
MaxSpeed_Z=5043
Accel_Z=20000
SpeedPercentage_Z=45
;X Axis
MaxSpeed_X=5046
Accel_X=20000
SpeedPercentage_X=48
;M3 Axis
MaxSpeed_M3=5048
Accel_M3=20000
SpeedPercentage_M3=49
;M4 Axis
MaxSpeed_M4=5048
Accel_M4=20000
SpeedPercentage_M4=49
;
[Sync]
;
HelixType=0
Revolutions=0.3
Distance=1.258
;
[Recip]
;
; 1: Equal Angle 2: Square 3: Sawtooth
Style=1
;Radial
Radial_Waves=5
Radial_Spindle_Degrees=18.124
Radial_Axis_Amplitude=4.258
;Axial
Axial_Waves=4
Axial_Spindle_Amplitude=22.258
Axial_Axis_Distance=7.896
RetroSpindleDistance=0
RetroAxisDistance=0
NoLastLeg=0
;
[GreekKey]
;
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
